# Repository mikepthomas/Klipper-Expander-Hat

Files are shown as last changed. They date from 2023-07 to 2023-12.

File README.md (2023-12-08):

# Klipper Fan Hat

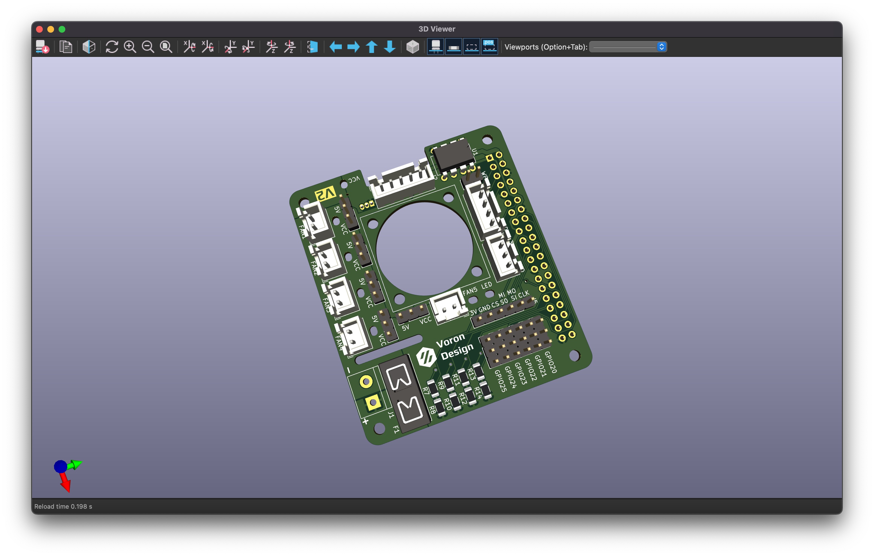
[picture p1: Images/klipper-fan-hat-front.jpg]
Klipper Fan Hat Front


[Interactive bom](https://klipper-fan-hat.mikethomas.info/)

### A Hat to use with the [Raspberry Pi as a Secondary MCU in Klipper](https://www.klipper3d.org/RPi_microcontroller.html):
- SKR Pico compatible input for powering the Pi and Serial communication
- 5 Mosfet outputs (with 2 pin JST-XH connectors standard on most fans used on 3D printers)
- Voltage selector jumpers to power each fan from either 5V or VCC supplied by screw terminal
- I2C and 1-Wire and SPI headers for connecting accesories to the Raspberry Pi
- 6 headers connected to General Purpose GPIO pins for accesories such as Filament Run Out Sensors
- On Board DS18B20 Temperature Sensor

### Documentation

[Documentation and Setup information here](Documentation/README.md)

 Parts that I sourced for assembly:
- 1206 Capacitor Set [Ali Express](https://www.aliexpress.com/item/1005002907508304.html)
- 1206 LEDs [Ali Express](https://www.aliexpress.com/item/1005003836509392.html)
- 1206 Resistor Set [Ali Express](https://www.aliexpress.com/item/33029877427.html)
- 2510 Axial Fan [Ali Express](https://www.aliexpress.com/item/32807610078.html)
- Blade Fuse Holder [Ali Express](https://www.aliexpress.com/item/1005003194700697.html)
- DIP-8 24C32 EEPROM [Ali Express](https://www.aliexpress.com/item/33036366759.html)
- DIP-8 Socket [Ali Express](https://www.aliexpress.com/item/1005001650813894.html)
- IRLML6344TRPBF Mosfets [Ali Express](https://www.aliexpress.com/item/1005004711783484.html)
- JST-XH Connector Set [Ali Express](https://www.aliexpress.com/item/33000442968.html)
- Jumper Caps [Ali Express](https://www.aliexpress.com/item/1005004482029258.html)
- KF301 Screw Terminal [Ali Express](https://www.aliexpress.com/item/1005003311688833.html)
- M2.5x14 BHCS [Ali Express](https://www.aliexpress.com/item/1005004123548619.html)
- Pin Header Set [Amazon](https://www.amazon.co.uk/gp/product/B07CWSXY7P)
- Raspberry Pi Headers and Spacers [Amazon](https://www.amazon.co.uk/gp/product/B07PHBTTGV)
- DS18B20 Temperature Sensor [Ali Express](https://www.aliexpress.com/item/1783091649.html)

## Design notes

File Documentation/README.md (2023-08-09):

- [Components](#components)
  - [Indicator LEDs](#indicator-leds)
  - [Power In](#power-in)
  - [Serial Header](#serial-header)
  - [I2C Header](#i2c-header)
  - [1-wire Header](#1-wire-header)
  - [GPIO Header](#gpio-header)
  - [SPI Header](#spi-header)
  - [Fan Mosfets](#fan-mosfets)
  - [DS18B20 Temperature Sensor](#ds18b20-temperature-sensor)
- [Setup](#setup)

# Components

## Indicator LEDs

There are 7 status indicator LEDs on the board:

- Status LED to indicate that the board is communicating with Klipper (LED)
- VCC status indicates that there is power present on the Vin and GND feeding the board through the screw terminals (J1)
- 5 Fan Status LEDs to indicate if the Fan Mosfets have power applied to them (FAN1-FAN5)

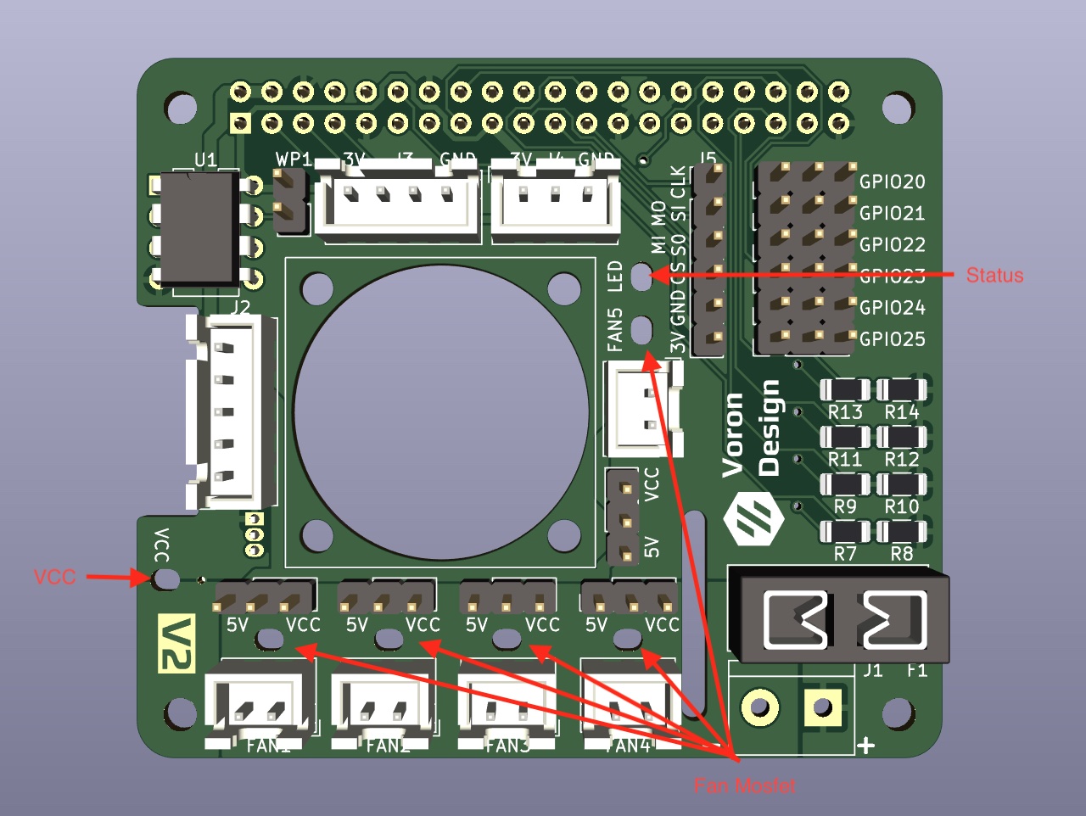
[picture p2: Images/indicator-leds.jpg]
Indicator LEDs


The Status LED is connected directly to GPIO16 with a current limiting resistor.

Indicator LEDs Schematic

Example klipper ready status configuration:

```bash
[static_digital_output status_led]
pins: rpi:gpio16
```

## Power In

VCC and GND are for feeding power to the Mosfets, this would typically be either 12V or 24V.

Power In

The fuse is a micro blade type fuse and should be chosen to the maximum draw of all of the MOSFET fed devices.

For example, if you are running a 40W heater, 2 5W fans and 1 2W fan, you will need a total of 62W of power. At 24V, this would translate to 62W/24V = 2.58A. The closest fuse might be a 5A fuse, which you should use.

Maximum power should not exceed 12A as the MOSFETs are each rated to a maximum of 3A.

Power In Schematic

## Serial Header

SKR Pico compatible interface, can be used to both power the Raspberry Pi and communicate with the MCU over Serial.

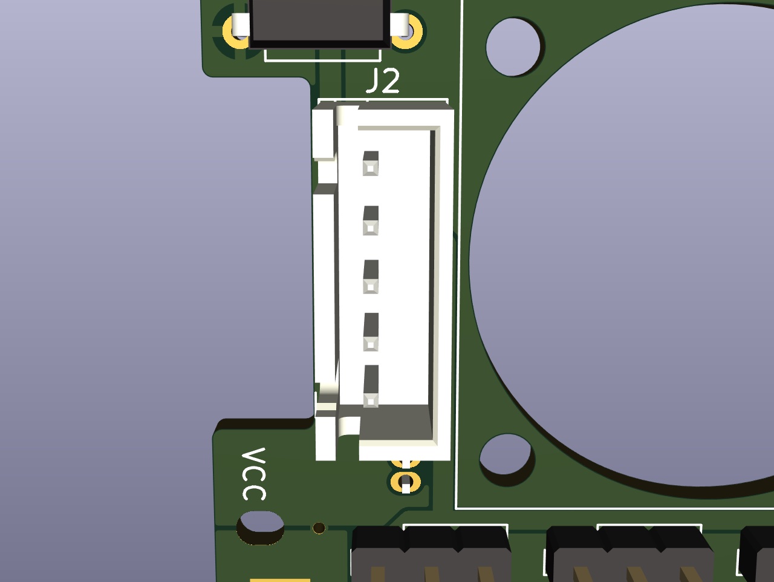
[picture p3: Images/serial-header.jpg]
Serial Header


The 5V pins are connected directly to the Raspberry Pi 5V pins and also supply 5V to the mosfet power selector headers.

Serial Header Schematic

## I2C Header

Contains a 3.3V I2C bus for connecting displays, and other sensors such as environemntal sensors and breakout expanders. This plugs into J3.

I2C Header

There are no Pull Up resistors on the I2C Bus as the Raspberry Pi already includes them.

I2C Header Schematic

Example display configuration:

```bash
[display]
lcd_type: sh1106
i2c_mcu: rpi
i2c_bus: i2c.1
```

Example HTU21D temperature sensor configuration:

```bash
[temperature_sensor enclosure_temp]
sensor_type: HTU21D
i2c_mcu: rpi
i2c_bus: i2c.1

[gcode_macro QUERY_ENCLOSURE]
gcode:
    {% set sensor = printer["htu21d enclosure_temp"] %}
    {action_respond_info(
        "Temperature: %.2f C\n"
        "Humidity: %.2f%%" % (
            sensor.temperature,
            sensor.humidity))}
```

## 1-wire Header

The 1-wire connector can be used for connecting 1-wire sensors or can also be used as another generic GPIO Header.

1-wire Header

The 1-wire pin, GPIO4 is pulled up to 3V3 with a 4.7k resistor.

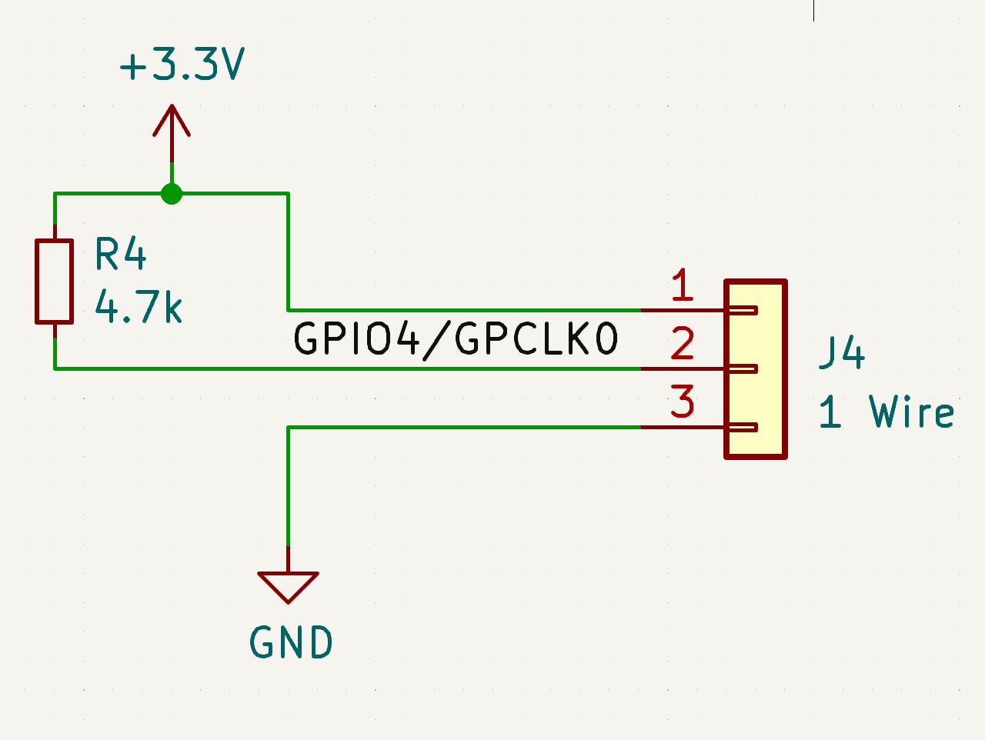
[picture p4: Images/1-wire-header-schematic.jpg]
1-wire Header Schematic


Example Output Pin configuration:

```bash
[output_pin gpio4]
pin: rpi:gpio4
value: 0
shutdown_value: 0
```

Example DS18B20 temperature sensor configuration:

```bash
[temperature_sensor enclosure_temp]
sensor_type: DS18B20
serial_no: 28-031674b175ff # Find with: ls /sys/bus/w1/devices/
ds18_report_time: 3.0 # Seconds between readings, minimum of 1.0
sensor_mcu: rpi
```

## GPIO Header

The GPIO headers GPIO20 - GPIO25 (GPIO, 3V3, GND) is available for creative uses.

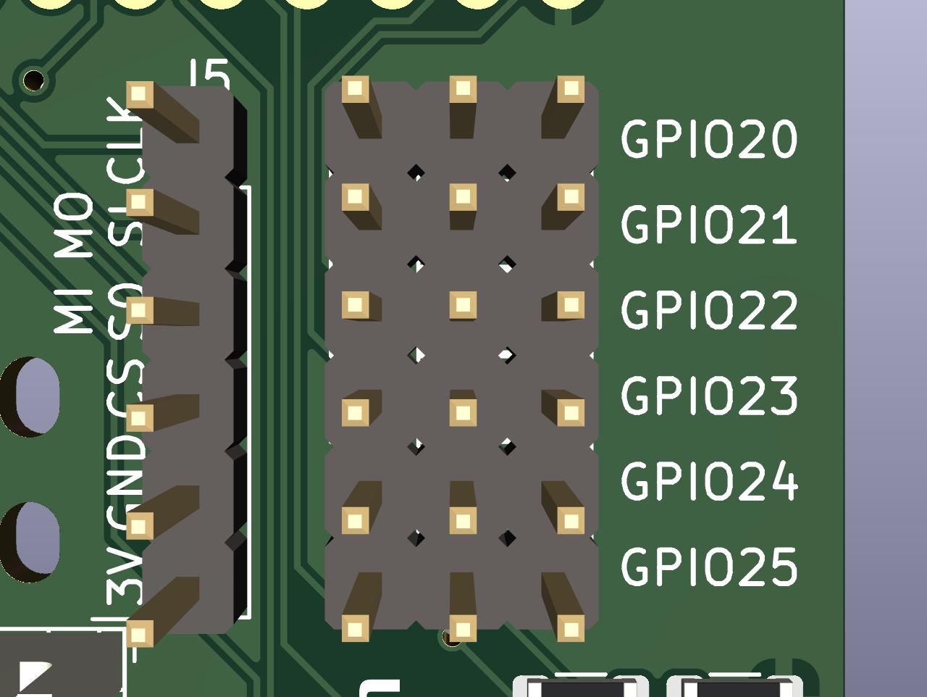
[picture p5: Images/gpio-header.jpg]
GPIO Header


Examples of what this can be used for include adding external mosfets, relays or a filament runout sensors.

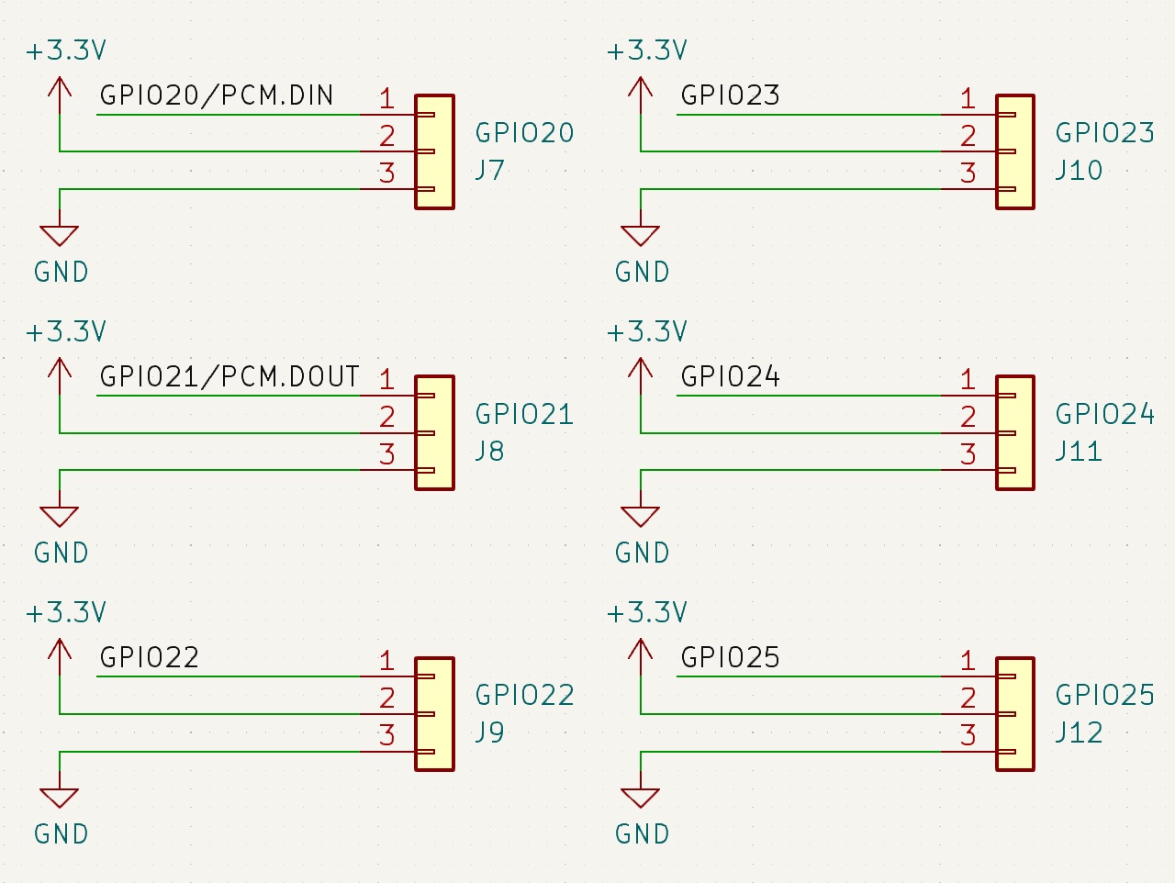
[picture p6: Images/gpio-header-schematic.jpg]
GPIO Header Schematic


Example Output Pin configuration:

```bash
[output_pin gpio20]
pin: rpi:gpio20
value: 0
shutdown_value: 0
```

Example Filament Sensor configuration:

```bash
[filament_switch_sensor filament_sensor]
pause_on_runout: true
switch_pin: ^!rpi:gpio20
```

## SPI Header

Contains a 3.3V SPI bus for connecting displays, and other sensors such as environmental sensors and breakout expanders. This plugs into J7.

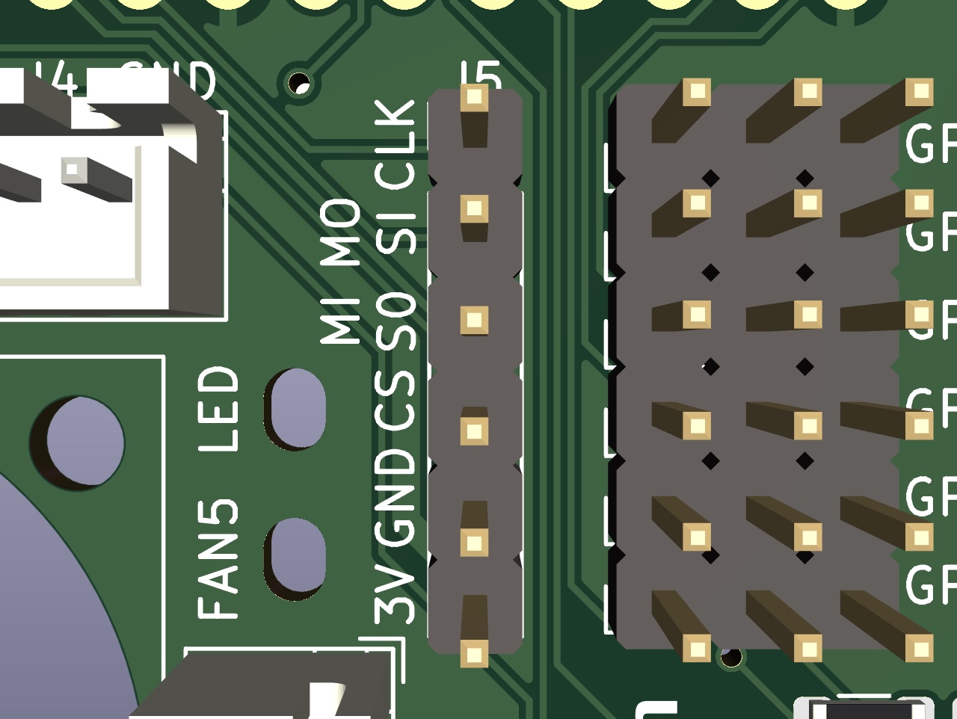
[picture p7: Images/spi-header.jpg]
SPI Header


This connects directly to the Raspberry Pi's SPI0 and uses CE0, CE1 is left unconnected.

SPI Header Schematic

Example AXDL345 configuration:

```bash
[adxl345]
cs_pin: rpi:None

[resonance_tester]
accel_chip: adxl345
probe_points: 150, 150, 20
```

## Fan Mosfets

5 x 3A mosfets for controlling LED's, Heater, Fans, and other accessories connected to pins GPIO12, GPIO13, GPIO17, GPIO18 and GPIO19.

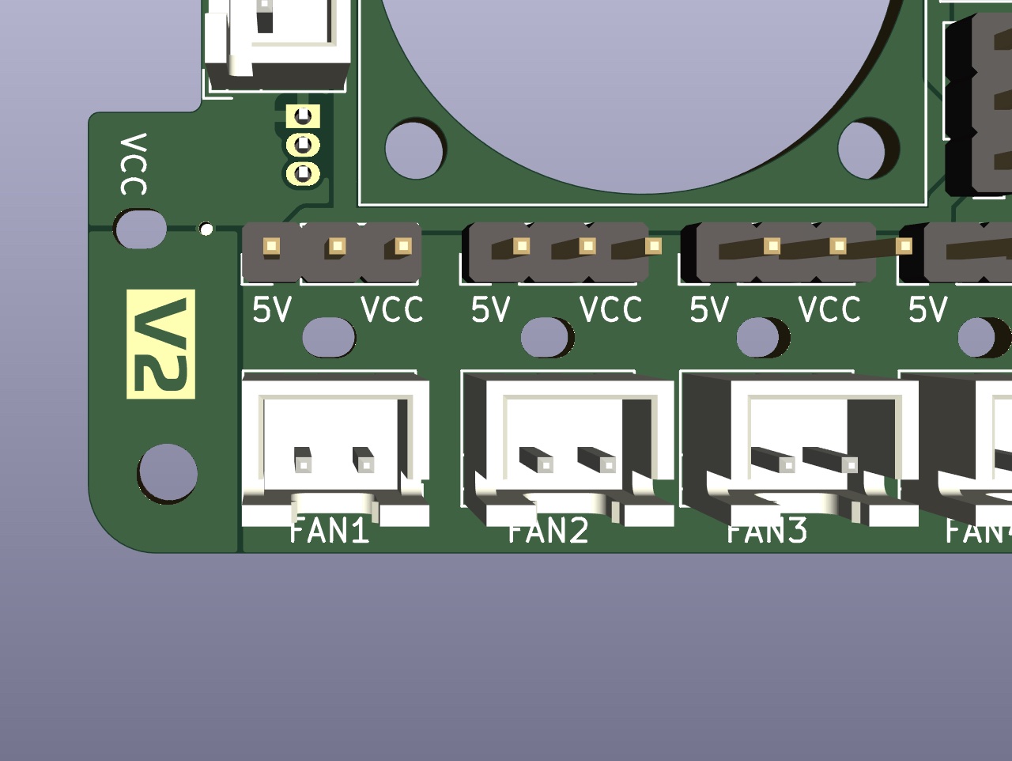
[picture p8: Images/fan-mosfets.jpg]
Fan Mosfets


The voltage selector header can be used to connect each mosfet to either the 5V rail or VCC.

Fan Mosfets Schematic

Example Output Pin configuration:

```bash
[output_pin mosfet1]
pin: rpi:gpio18
value: 0
shutdown_value: 0
```

Example Fan configuration:

```bash
[fan_generic fan1]
pin: rpi:gpio18
```

Example Hardware PWM Fan configuration:

```bash
[fan_generic fan1]
pin: rpi:pwmchip0/pwm0
hardware_pwm: true
```

# DS18B20 Temperature Sensor

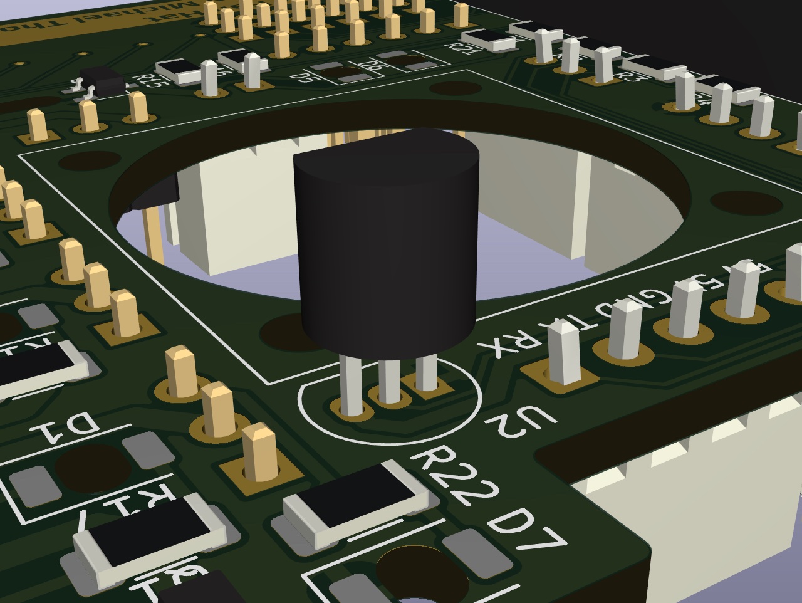
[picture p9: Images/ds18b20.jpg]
DS18B20 Schematic


An example config to set up the Temperature sensor is available in the [1-wire Header](#1-wire-header) section.

DS18B20 Schematic

# Setup

If you purchased your board already assembled, it is likely that the hat EEPROM has already been flashed. However, if you are building it yourself you will need [Flash the EEPROM by following this guide](../EEPROM/README.md).

You should just be able to go through the [Klipper RPi micro-controller setup guide](https://www.klipper3d.org/RPi_microcontroller.html), and that page will be the most up-to-date with the latest Klipper version.

## Install the RC Script

If you want to use the host as a secondary MCU the klipper_mcu process must run before the klippy process.

After installing Klipper, install the script. run:

```bash
cd ~/klipper/
sudo cp ./scripts/klipper-mcu.service /etc/systemd/system/
sudo systemctl enable klipper-mcu.service
```

## Building the Micro-Controller Code

To compile the Klipper micro-controller code, start by configuring it for the `Linux process`:

```bash
cd ~/klipper/
make menuconfig
```

In the menu, set `Micro-controller Architecture` to `Linux process`, then save and exit.

Klipper Config

To build and install the new micro-controller code, run:

```bash
sudo service klipper stop
make flash
sudo service klipper start
```

If klippy.log reports a `Permission denied` error when attempting to connect to `/tmp/klipper_host_mcu` then you need to add your user to the tty group. The following command will add the `pi` user to the `tty` group:

```bash
sudo usermod -a -G tty pi
```

## Remaining configuration

You can copy the config from the EEPROM chip of the hat into the Klipper config directory:

```bash
cat /proc/device-tree/hat/custom_1 > ~/printer_data/config/klipper-fan-hat.cfg
```

## Optional: Enabling SPI

SPI should be enabled automatically by the hat EEPROM, If you have trouble, you can enable it manually by running `sudo raspi-config` and enabling SPI under the `Interfacing options` menu.

Enable SPI

## Optional: Enabling I2C

I2C should be enabled automatically by the hat EEPROM, If you have trouble, you can enable it manually by running `sudo raspi-config` and enabling I2C under the `Interfacing options` menu.

Enable I2C

If planning to use I2C for the MPU accelerometer, it is also required to set the baud rate to 400000 by: adding/uncommenting `dtparam=i2c_arm=on,i2c_arm_baudrate=400000` in `/boot/config.txt` (or `/boot/firmware/config.txt` in some distros).
This should also be automatically be enabled by the hat EEPROM however you can do it manually if you have any problems.

## Optional: Enabling 1-wire

If you require, you can enable the 1-wire interface by running `sudo raspi-config` and enabling 1-wire under the `Interfacing options` menu.

Enable 1-wire

you can then find any conneted sensors serial numbers with: `ls /sys/bus/w1/devices/`

## Optional: Hardware PWM

Raspberry Pi's have two PWM channels (PWM0 and PWM1) which are exposed on the header or if not, can be routed to existing gpio pins. The Linux mcu daemon uses the pwmchip sysfs interface to control hardware pwm devices on Linux hosts. The pwm sysfs interface is not exposed by default on a Raspberry and can be activated by adding a line to `/boot/config.txt`:

```bash
# Enable pwmchip sysfs interface
dtoverlay=pwm,pin=12,func=4
```

This example enables only PWM0 and routes it to gpio12. If both PWM channels need to be enabled you can use `pwm-2chan`:

```bash
# Enable pwmchip sysfs interface
dtoverlay=pwm-2chan,pin=12,pin2=13,func=4,func2=4
```

The overlay does not expose the pwm line on sysfs on boot and needs to be exported by echo'ing the number of the pwm channel to `/sys/class/pwm/pwmchip0/export`:

```bash
echo 0 > /sys/class/pwm/pwmchip0/export
```

If you have enabled `pwm-2chan` you can enable PWM1 too with:

```bash
echo 1 > /sys/class/pwm/pwmchip0/export
```

This will create device `/sys/class/pwm/pwmchip0/pwm0` and optionally `/sys/class/pwm/pwmchip0/pwm1` in the filesystem. The easiest way to do this is by adding them to `/etc/rc.local` before the `exit 0` line.

With the sysfs in place, you can now use either the pwm channel(s) by adding the following piece of configuration to your `klipper-fan-hat.cfg`:

```bash
[fan_generic fan1]
pin: rpi:pwmchip0/pwm0
hardware_pwm: true
cycle_time: 0.000001
```

This will add hardware pwm control to gpio12 on the Pi (because the overlay was configured to route pwm0 to pin=12).

PWM0 can be routed to gpio12 and gpio18, PWM1 can be routed to gpio13 and gpio19:

| PWM | gpio PIN | Func |
| --- | --- | ---- |
| 0 | 12 | 4 |
| 0 | 18 | 2 |
| 1 | 13 | 4 |
| 1 | 19 | 2 |

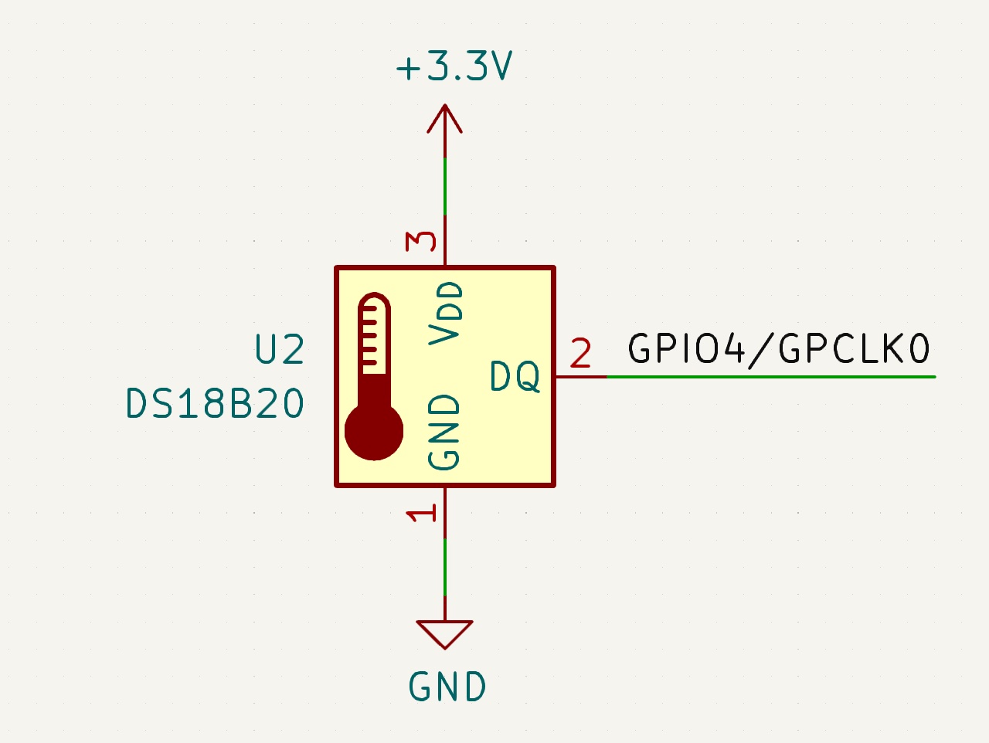
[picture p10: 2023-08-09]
Images/ds18b20-schematic.jpg

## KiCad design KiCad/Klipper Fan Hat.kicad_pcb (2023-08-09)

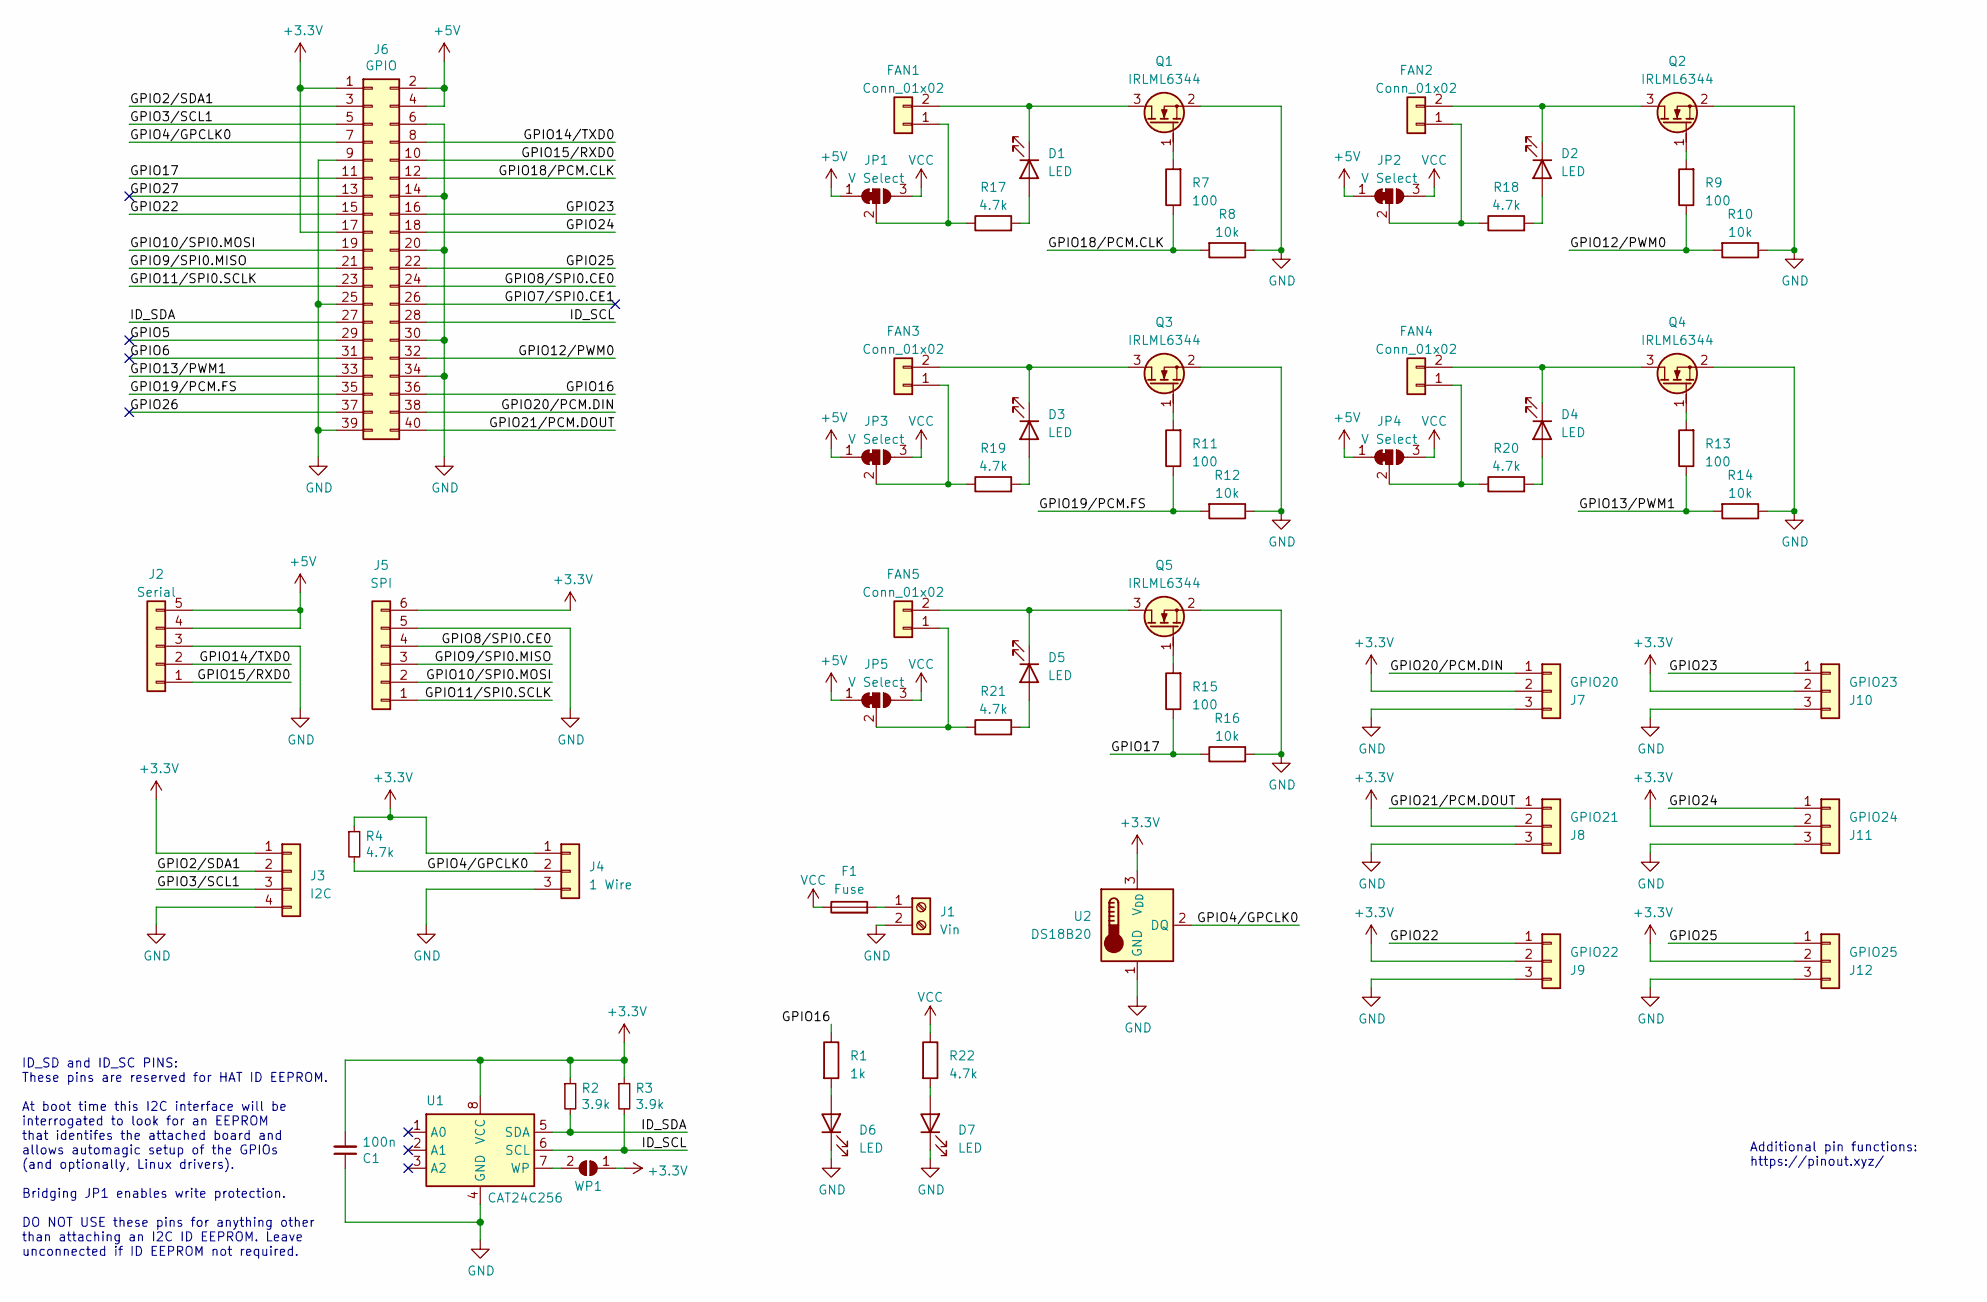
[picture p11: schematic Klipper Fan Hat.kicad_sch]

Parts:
C1: 100n; C_1206_3216Metric
D1, D2, D3, D4, D5, D6, D7: LED; LED_1206_3216Metric_ReverseMount_Hole1.8x2.4mm
F1: Fuse; Fuseholder_Blade_Mini_Keystone_3568
FAN1, FAN2, FAN3, FAN4, FAN5: Conn_01x02; JST_XH_B2B-XH-A_1x02_P2.50mm_Vertical
GPIO20: J7; PinHeader_1x03_P2.54mm_Vertical
GPIO21: J8; PinHeader_1x03_P2.54mm_Vertical
GPIO22: J9; PinHeader_1x03_P2.54mm_Vertical
GPIO23: J10; PinHeader_1x03_P2.54mm_Vertical
GPIO24: J11; PinHeader_1x03_P2.54mm_Vertical
GPIO25: J12; PinHeader_1x03_P2.54mm_Vertical
J1: Vin; TerminalBlock_bornier-2_P5.08mm
J2: Serial; JST_XH_B5B-XH-A_1x05_P2.50mm_Vertical
J3: I2C; JST_XH_B4B-XH-A_1x04_P2.50mm_Vertical
J4: 1 Wire; JST_XH_B3B-XH-A_1x03_P2.50mm_Vertical
J5: SPI; PinHeader_1x06_P2.54mm_Vertical
J6: GPIO; PinSocket_2x20_P2.54mm_Vertical
JP1, JP2, JP3, JP4, JP5: V Select; PinHeader_1x03_P2.54mm_Vertical
Q1, Q2, Q3, Q4, Q5: IRLML6344; TSOT-23
R1: 1k; R_1206_3216Metric
R2, R3: 3.9k; R_1206_3216Metric
R4, R17, R18, R19, R20, R21, R22: 4.7k; R_1206_3216Metric
R7, R9, R11, R13, R15: 100; R_1206_3216Metric
R8, R10, R12, R14, R16: 10k; R_1206_3216Metric
U1: CAT24C256; DIP-8_W7.62mm
U2: DS18B20; TO-92_Inline
WP1: ID_WP; PinHeader_1x02_P2.54mm_Vertical

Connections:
+3V3: C1.2, GPIO20.2, GPIO21.2, GPIO22.2, GPIO23.2, GPIO24.2, GPIO25.2, J3.1, J4.1, J5.6, J6.1, J6.17, R2.1, R3.1, R4.1, U1.8 (VCC), U2.3 (V_{DD}), WP1.1 (A)
+5V: J2.4, J2.5, J6.2, J6.4, JP1.1 (A), JP2.1 (A), JP3.1 (A), JP4.1 (A), JP5.1 (A)
/GPIO2/SDA1: J3.2, J6.3
/GPIO3/SCL1: J3.3, J6.5
/GPIO4/GPCLK0: J4.2, J6.7, R4.2, U2.2 (DQ)
/GPIO5: J6.29
/GPIO6: J6.31
/GPIO7/SPI0.CE1: J6.26
/GPIO8/SPI0.CE0: J5.4, J6.24
/GPIO9/SPI0.MISO: J5.3, J6.21
/GPIO10/SPI0.MOSI: J5.2, J6.19
/GPIO11/SPI0.SCLK: J5.1, J6.23
/GPIO12/PWM0: J6.32, R9.1, R10.2
/GPIO13/PWM1: J6.33, R13.1, R14.2
/GPIO14/TXD0: J2.2, J6.8
/GPIO15/RXD0: J2.1, J6.10
/GPIO16: J6.36, R1.1
/GPIO17: J6.11, R15.1, R16.1
/GPIO18/PCM.CLK: J6.12, R7.1, R8.2
/GPIO19/PCM.FS: J6.35, R11.1, R12.2
/GPIO20/PCM.DIN: GPIO20.1, J6.38
/GPIO21/PCM.DOUT: GPIO21.1, J6.40
/GPIO22: GPIO22.1, J6.15
/GPIO23: GPIO23.1, J6.16
/GPIO24: GPIO24.1, J6.18
/GPIO25: GPIO25.1, J6.22
/GPIO26: J6.37
/GPIO27: J6.13
/ID_SCL: J6.28, R3.2, U1.6 (SCL)
/ID_SDA: J6.27, R2.2, U1.5 (SDA)
GND: C1.1, D6.1 (K), D7.1 (K), GPIO20.3, GPIO21.3, GPIO22.3, GPIO23.3, GPIO24.3, GPIO25.3, J1.2, J2.3, J3.4, J4.3, J5.5, J6.6, J6.9, J6.14, J6.20, J6.25, J6.30, J6.34, J6.39, Q1.2 (S), Q2.2 (S), Q3.2 (S), Q4.2 (S), Q5.2 (S), R8.1, R10.1, R12.1, R14.1, R16.2, U1.4 (GND), U2.1 (GND)
unnamed: D1.2 (A), R17.2
unnamed: D1.1 (K), FAN1.2, Q1.3 (D)
unnamed: D2.2 (A), R18.2
unnamed: D2.1 (K), FAN2.2, Q2.3 (D)
unnamed: D3.2 (A), R19.2
unnamed: D3.1 (K), FAN3.2, Q3.3 (D)
unnamed: D4.2 (A), R20.2
unnamed: D4.1 (K), FAN4.2, Q4.3 (D)
unnamed: D5.2 (A), R21.2
unnamed: D5.1 (K), FAN5.2, Q5.3 (D)
unnamed: D6.2 (A), R1.2
unnamed: D7.2 (A), R22.2
unnamed: FAN1.1, JP1.2 (C), R17.1
unnamed: FAN2.1, JP2.2 (C), R18.1
unnamed: FAN3.1, JP3.2 (C), R19.1
unnamed: FAN4.1, JP4.2 (C), R20.1
unnamed: FAN5.1, JP5.2 (C), R21.1
unnamed: F1.2, J1.1
unnamed: Q1.1 (G), R7.2
unnamed: Q2.1 (G), R9.2
unnamed: Q3.1 (G), R11.2
unnamed: Q4.1 (G), R13.2
unnamed: Q5.1 (G), R15.2
unnamed: U1.7 (WP), WP1.2 (B)
VCC: F1.1, JP1.3 (B), JP2.3 (B), JP3.3 (B), JP4.3 (B), JP5.3 (B), R22.1

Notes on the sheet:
Additional pin functions: https://pinout.xyz/
ID_SD and ID_SC PINS: These pins are reserved for HAT ID EEPROM. At boot time this I2C interface will be interrogated to look for an EEPROM that identifes the attached board and allows automagic setup of the GPIOs (and optionally, Linux drivers). Bridging JP1 enables write protection. DO NOT USE th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

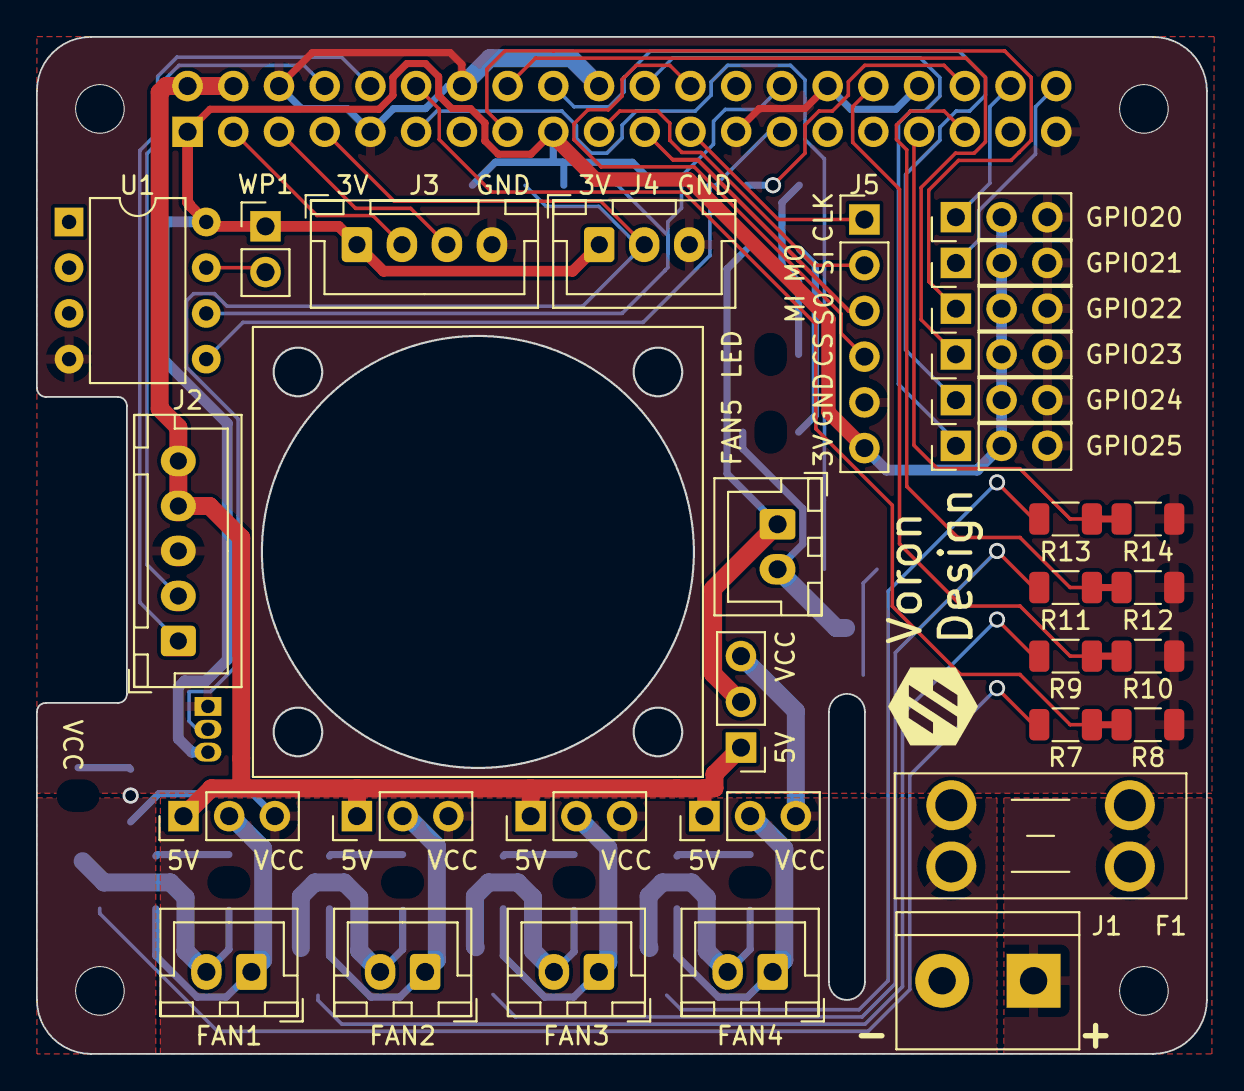
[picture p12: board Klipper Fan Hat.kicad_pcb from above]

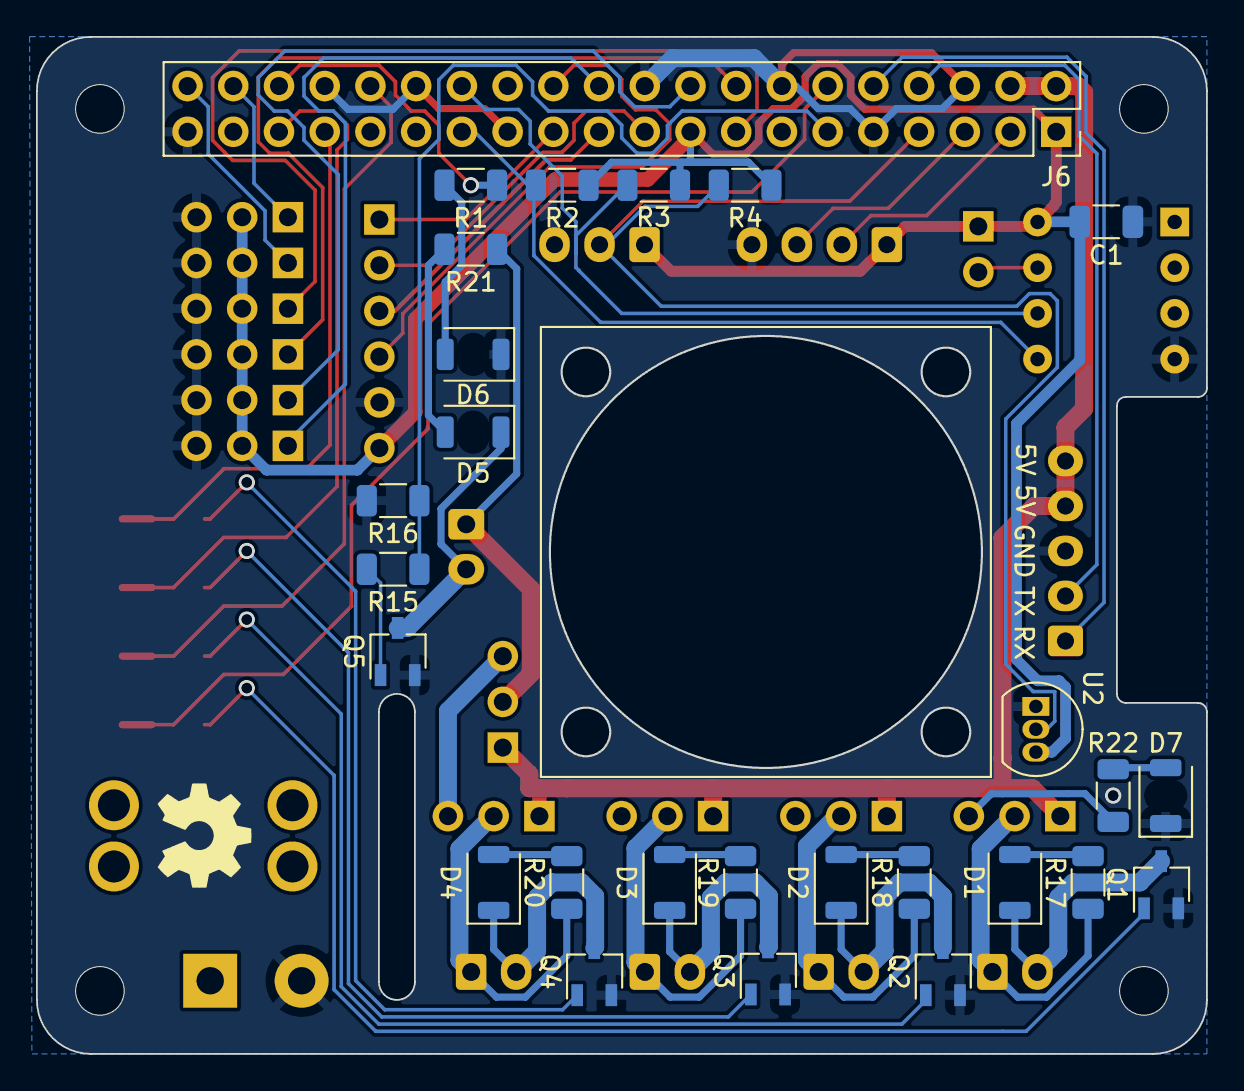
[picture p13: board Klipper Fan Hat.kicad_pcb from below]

Board: 2 copper layers, 65.0 x 56.5 mm, 63 parts (27 on the bottom side), 51 nets.

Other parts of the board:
MH1, MH2, MH3, MH4: MountingHole_2.7mm_M2.5

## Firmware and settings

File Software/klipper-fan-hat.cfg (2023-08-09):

[mcu rpi]
#####################################################################
# Compile the Klipper micro-controller code for "Linux process"
#####################################################################
serial: /tmp/klipper_host_mcu
##--------------------------------------------------------------------

[static_digital_output status_led]
pins: rpi:gpio16

#####################################################################
#      Fans
#####################################################################

# For hardware PWM add one of the following to `/boot/config.txt`:
# dtoverlay=pwm-2chan,pin=18,pin2=19,func=2,func2=2
# dtoverlay=pwm-2chan,pin=12,pin2=13,func=4,func2=4

# add the following to /etc/rc.local before exit 0:
# echo 0 > /sys/class/pwm/pwmchip0/export
# echo 1 > /sys/class/pwm/pwmchip0/export

# Then enable `hardware_pwm` on the selected pins

[fan_generic fan1]
pin: rpi:gpio18
#pin: rpi:pwmchip0/pwm0
hardware_pwm: false

[fan_generic fan2]
pin: rpi:gpio12
#pin: rpi:pwmchip0/pwm0
hardware_pwm: false

[fan_generic fan3]
pin: rpi:gpio19
#pin: rpi:pwmchip0/pwm1
hardware_pwm: false

[fan_generic fan4]
pin: rpi:gpio13
#pin: rpi:pwmchip0/pwm1
hardware_pwm: false

# Control the Pi fan by host temperature
[temperature_fan raspberry_pi]
pin: rpi:gpio17
sensor_type: temperature_host
min_temp: 10
max_temp: 100
target_temp: 35
control: pid
pid_kp: 1.0
pid_ki: 0.5
pid_kd: 2.0

#####################################################################
#      I2C
#####################################################################

# Example1: Using the I2C bus with an OLED Display
#[display]
#lcd_type: sh1106
#i2c_mcu: rpi
#i2c_bus: i2c.1
#x_offset: 1 # Shift the display towards the right
# If not using GPIO pins below you can attach a rotary encoder:
#click_pin: ^!rpi:gpio4
#encoder_pins: ^rpi:gpio5, ^rpi:gpio6

# Example2: Using the I2C bus to read a HTU21D sensor
#[temperature_sensor enclosure_temp]
#sensor_type: HTU21D
#i2c_mcu: rpi
#i2c_bus: i2c.1

#[gcode_macro QUERY_ENCLOSURE]
#gcode:
#    {% set sensor = printer["htu21d enclosure_temp"] %}
#    {action_respond_info(
#        "Temperature: %.2f C\n"
#        "Humidity: %.2f%%" % (
#            sensor.temperature,
#            sensor.humidity))}

#####################################################################
#      1-wire & GPIO
#####################################################################

# GPIO4 is the default pin for 1-Wire sensors
[output_pin gpio4]
pin: rpi:gpio4
value: 0
shutdown_value: 0

# Example1: Using 1-wire DS18B20 temperature sensor
# To enable 1-wire add the following to `/boot/config.txt`:
# dtoverlay=w1-gpio
#[temperature_sensor enclosure_temp]
#sensor_type: DS18B20
#serial_no: 28-031674b175ff # Find with: ls /sys/bus/w1/devices/
#ds18_report_time: 3.0 # Seconds between readings, minimum of 1.0
#sensor_mcu: rpi

[output_pin gpio20]
pin: rpi:gpio20
value: 0
shutdown_value: 0

# Example2: Using pin as filament sensor
#[filament_switch_sensor filament_sensor]
#pause_on_runout: true
#switch_pin: ^!rpi:gpio20

#####################################################################
#      SPI
#####################################################################

# Example: Using the SPI bus of the RPi with an AXDL345 Accelerometer
#[adxl345]
#cs_pin: rpi:None

#[resonance_tester]
#accel_chip: adxl345
#probe_points: 150, 150, 20 # an example

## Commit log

2023-07-21 update values of pull up resistors
    [Klipper Fan Hat.kicad_pcb, Klipper Fan Hat.kicad_sch]
2023-08-09 Update KlippUpdate Klipper Fan Hat to expose more GPIO pins and add an on board DS18B20 Temperature Sensor
    [Klipper Fan Hat-B_Cu.gbl, Klipper Fan Hat-B_Mask.gbs, Klipper Fan Hat-B_Silkscreen.gbo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]
2023-08-09 Update Serial Header Ground connection
    [Klipper Fan Hat-B_Cu.gbl, Klipper Fan Hat-B_Mask.gbs, Klipper Fan Hat-B_Silkscreen.gbo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]
2023-08-09 Add correct Gerber files
    [Klipper Fan Hat-B_Cu.gbl, Klipper Fan Hat-B_Mask.gbs, Klipper Fan Hat-B_Silkscreen.gbo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]
2023-12-08 Update link to interactive BOM

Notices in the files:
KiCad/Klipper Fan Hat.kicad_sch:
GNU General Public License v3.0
